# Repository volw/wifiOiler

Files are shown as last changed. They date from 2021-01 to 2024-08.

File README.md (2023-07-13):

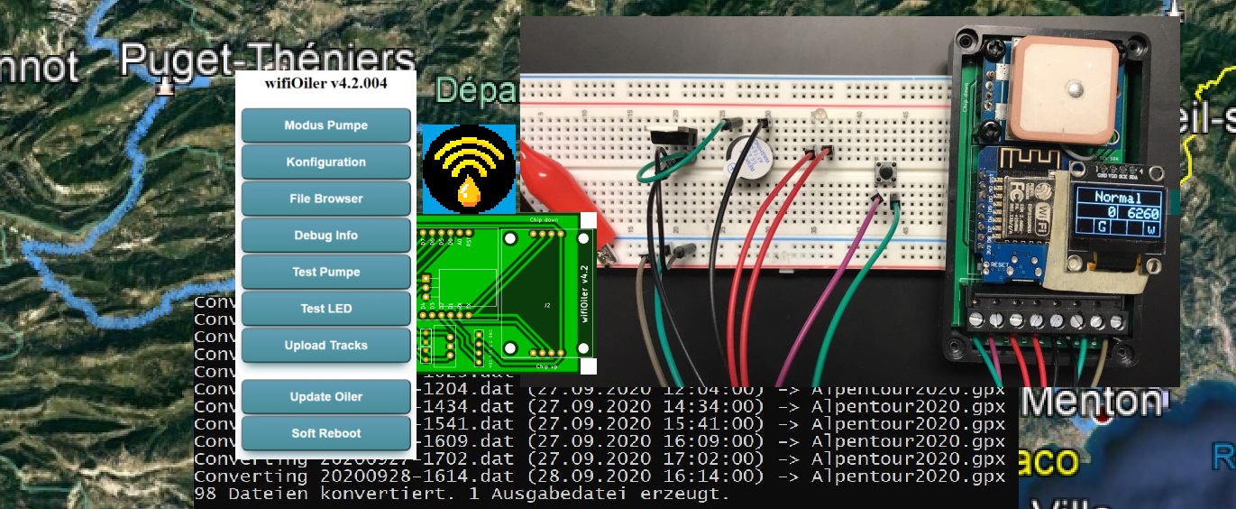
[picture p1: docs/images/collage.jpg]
wifioiler_collage


# wifiOiler

Automatischer streckenabhängiger Kettenöler für's Motorrad mit folgenden Funktionen:

- Ermittlung der zurückgelegten Strecke per GPS.
- Auslösen eines Ölvorgangs nach einer einstellbaren Anzahl von Metern.
- Drei verschiedene Distanzen oder Modi einstellbar (Normal, Regen, Offroad). 
- Notlaufprogramm = zeitabhängiges Ölen, falls kein GPS Signal empfangen werden kann.
- Bedienung über Button, Feedback per zweifarbiger LED.
- Erweiterte Bedienung über jedes internetfähige Gerät, auf dem ein Internet Browser läuft, z.B. Handy, Notebook, etc..
- Der Öler kann sich in ein bestehendes WLAN einklinken oder selber einen Access Point erstellen.
- WiFi kann jederzeit an- oder ausgestellt werden (während der Fahrt wird WiFi automatisch abgeschaltet).
- Aufzeichnung der gefahrenen Strecken im Speicher (LittleFS-Dateisystem) des verwendeten ESP8266 Chips (Platz für ca. 45 Stunden Fahrzeit vorhanden).
- Übertragen (und löschen) der aufgezeichneten Strecken per WLAN auf einen zentralen Web-Server (s. Oilerbase auf Basis eines Raspberry Pis, Strecken können auch manuell heruntergeladen werden).
- Herunterladen von Updates von einem zentralen Web-Server (s. Oilerbase). Updates können auch per Upload ausgelöst werden.
- PHP Skripte und html Dateien für den zentralen Web-Server (Apache auf Raspberry Pi, s. Oilerbase)
- Software zur Konvertierung der aufgezeichneten Tracks in das .gpx Format (können dann z.B. auf Google Earth angezeigt werden).

In diesem Repo zu finden:

- Schaltplan und Teileliste zur Erstellung und Bestückung der Platine.
- Vorschläge für Bauteile zum Einbau in das Motorrad.
- Komplette Software für Öler, Oilerbase und Track Konvertierung.
- Anleitungen für Aufbau, Inbetriebnahme und Bedienung (s. "docs").
- Einbauvorschlag.

Wem das alles zuviel an Bastelei ist und Hilfe bei Erstellung der Platine, bzw. Steuereinheit benötigt, kann sich gerne melden...

## Credits

Detlev Axon, creator of [RehOiler](https://www.rehtronik.de/startseite1.html)

Mikal Hart, creator of [TinyGPS++](https://github.com/mikalhart/TinyGPSPlus), an NMEA parsing library.

Hristo Gochkov for the FSBrowser example.

Maarten Lamers for his distance calculation (taken from TinyGPS++)

Patrick Gillespie for his [Macro Font Generator](http://patorjk.com/software/taag).

And many thanks to all the others who share their knowledge

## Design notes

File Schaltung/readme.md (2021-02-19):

# Schaltung

Die Schaltung wurde zuletzt mit KiCad 5.1.9_1 bearbeitet. Alle Symbole und Footprints wurden lokal verlinkt und sind in den Verzeichnissen enthalten (Symbole in wifiOilerLib.lib, Footprints in ProjectFootprints.pretty).

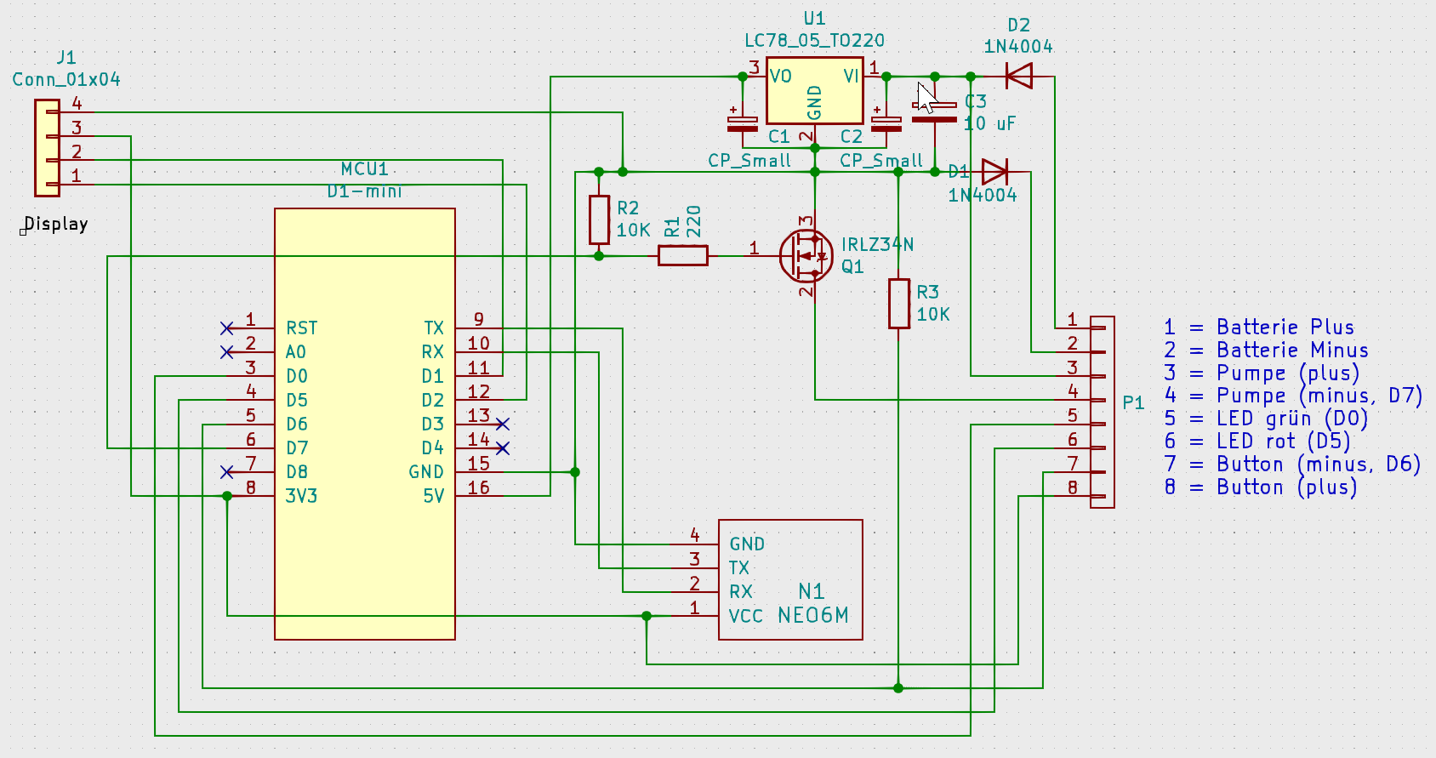
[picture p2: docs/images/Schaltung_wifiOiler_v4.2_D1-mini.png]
Schaltung wifiOiler v4.2 D1-mini


Abstände und Leiterbahnen wurden großzügig ausgelegt, um Fräsen und Löten zu erleichtern.

Noch ist eine Leiterbahn auf der zweiten Seite vorhanden, die aber auch noch eliminiert werden kann, wenn die Leiterbahnen, die zum Displayanschluss führen, etwas umgeroutet werden. Für eine Auftragsfertigung ist es fast egal, ob ein- oder zweiseitig, da viele Fertiger einseitige Platinen gar nicht mehr anbieten. Möchte man die Platine selber fräsen, sollte sie natürlich einseitig sein. Hier die Änderung, die dazu notwendig wäre (oben die aktuelle Ansicht, darunter die Änderung)

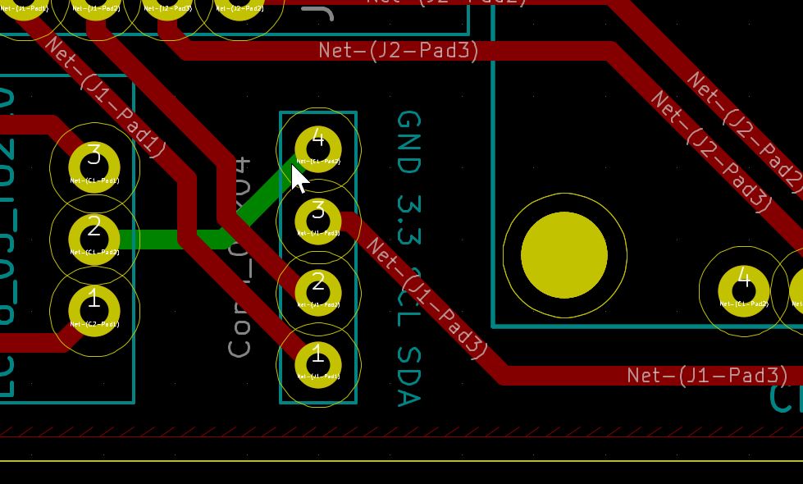
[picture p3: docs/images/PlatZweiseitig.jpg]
Platine zweiseitig
 

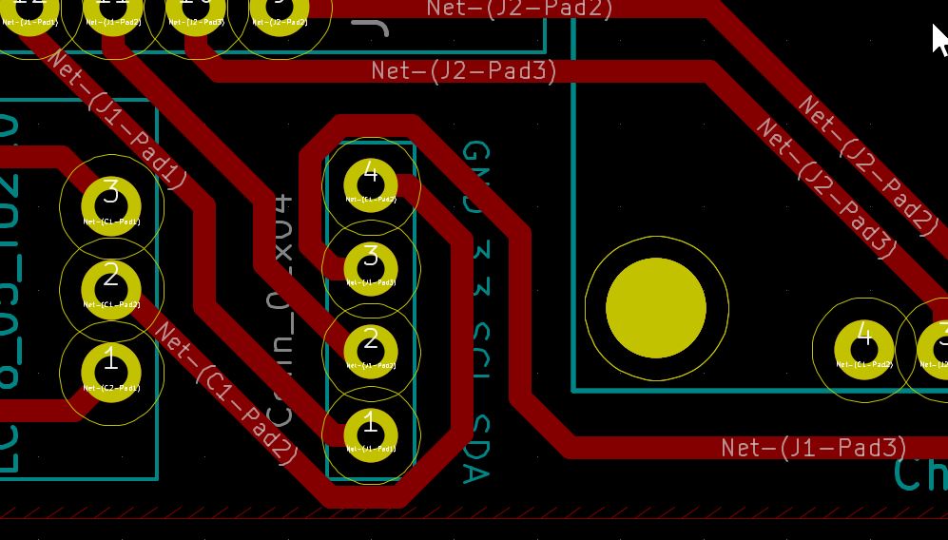
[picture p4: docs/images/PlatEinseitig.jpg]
Platine einseitig


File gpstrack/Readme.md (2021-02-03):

# wifiOiler GPX Converter

Die Fahrstrecken werden vom Öler in einem eigenen Format aufgezeichnet.

Mit diesem Tool können die Track-Dateien in das GPX Format konvertiert werden. Dann lassen sie sich z.B. in Google Earth anzeigen. Um das Projekt zu kompilieren, bzw. zu erstellen, wird Visual Studio benötigt (z.B. das kostenfrei nutzbare Visual Studio Community). 

**Syntax:** `gpstrack.exe [Quelle [Ziel]] [/o(verwrite)] [/d(aily)] [/r(ename)]`

Dabei bedeuten:

**Quelle:** ein Verzeichnis oder Suchmuster für Dateien, wie z.B. "D:\Touren\August" oder "202108*.dat". Wird als Quelle ein Verzeichnis angegeben, wird versucht, alle Dateien in diesem Verzeichnis mit der Endung .dat zu konvertieren.

**Ziel:** ist das Ziel ein existierendes Verzeichnis, werden die erzeugten .gpx Dateien in dieses Verzeichnis geschrieben. Existiert das Ziel dagegen nicht, wird als Ziel eine Datei angenommen und die Quelldateien werden in dieser Zieldatei zusammengefasst. Wenn kein Ziel angegeben wird, werden die Ausgabedateien in das Quellverzeichnis geschrieben.

**/o(verwrite):** wird diese Option angegeben, werden existierende Zieldateien ohne Nachfrage überschrieben. Die Option kann vollständig oder teilweise angegeben werden (also "/o" oder  "/overwrite" oder allen Zwischenformen).

**/d(aily):** wird diese Option angegeben, werden Dateien auf Tagesbasis zusammengefasst. Die Zieldateien haben als Namen das Tagesdatum in der Form JJJJMMTT.gpx. Diese Option hat keine Wirkung, wenn als Ziel eine Ausgabedatei angegeben wurde.

**/r(ename):** eigentlich nicht mehr relevant. In der Vergangenheit kam es schon mal vor, dass das Datum im Dateinamen vom ersten Datum in der Datei abwich. Diese Option hat das nachträglich korrigiert. War der Dateiname z.B: "000000-1435.dat", versucht das Programm, ein gültiges Datum in den GPS Daten in der Datei zu finden und den Dateinamen damit zu "reparieren".

### Beispiele

**`gpstrack`** alle Dateien im aktuellen Verzeichnis mit der Endung .dat werden konvertiert in Dateien mit der Endung .gpx.

**`gpstrack D:\temp /d`** alle Dateien im Verzeichnis D:\temp (mit Endung *.dat) werden auf Tagesbasis zusammengefasst und in das Verzeichnis D:\temp geschrieben (mit Endung .gpx)

**`gpstrack . Alpentour2020.gpx /o`** alle Dateien aus dem aktuellen Verzeichnis (s. den Punkt) werden in einer Zieldatei mit Namen "Alpentour2020.gpx" zusammengefasst. Falls die Datei schon existiert, wird sie überschrieben. Die Ausgabe dabei sieht etwa so aus (Ausschnitt):

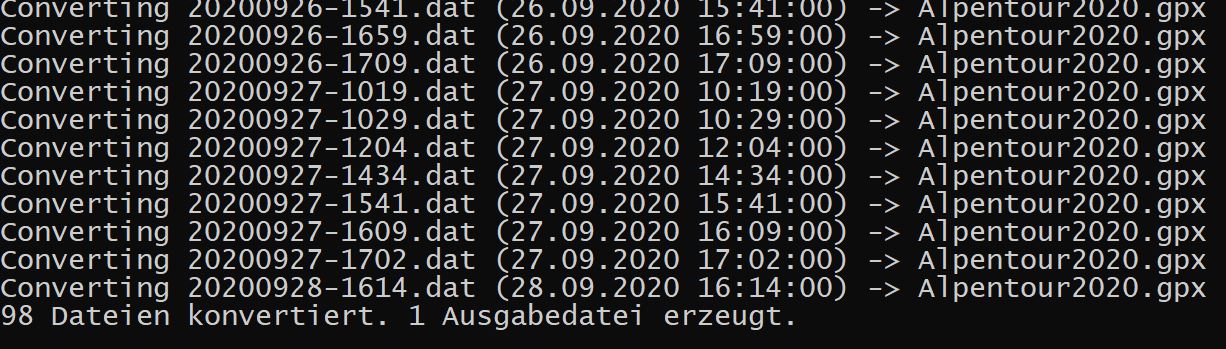
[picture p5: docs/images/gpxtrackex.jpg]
Ausgabe Alt-Text


Und das Ergebnis in Google Earth (beim Öffnen Dateityp .gpx wählen):

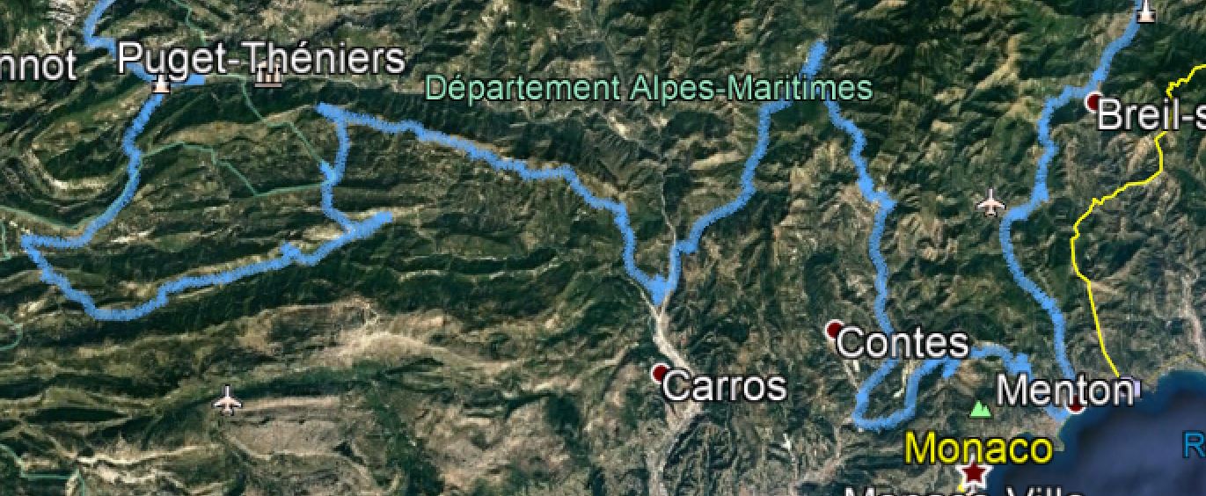
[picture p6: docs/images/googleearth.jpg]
Anzeige in Google Earth


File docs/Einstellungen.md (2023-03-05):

# Einstellungen
Hier werden die Einstellungen des Ölers beschrieben, die über die Web-Oberfläche geändert werden können. 
Die Einstellungen werden in der Datei **oiler.ini** in lesbarer Form gespeichert. 
Die Datei kann auch mit einem Editor bearbeitet werden, bevor sie hochgeladen wird. 
Geänderte Einstellungen, die über die Web Oberfläche geändert wurden, sind nach dem Speichern sofort aktiv. 
Dies gilt nicht für die Logging Einstellungen, die GPS-Konfigurationsdatei und die Einstellung für automatischen WiFi-Start. 
Um diese Einstellungen zu aktivieren, muss der Öler durchgestartet werden. 
Um geänderte Einstellungen zu aktivieren, die über den integrierten Editor geändert (oder mit der Upload-Funktion hochgeladen) wurden, muss der Öler neu gestartet werden.
<br>Folgende Einstellungen können angepasst werden:
## Wartezeit Simulation
Dieser Wert in Sekunden gibt an, ab wann das Notfallprogramm aktiv werden soll, wenn kein GPS Signal empfangen wird. Bei einem Wert von z.B. 180 wird 3 Minuten nach dem Start des Ölers (wenn bis dahin kein gültiges GPS Signal empfangen werden konnte) eine bestimmte Geschwindigkeit angenommen. Diese simulierte Geschwindigkeit wird durch den Wert **Meter/s bei Simulation** bestimmt. Beispielrechnung: wenn der Wert **Normal Mode Meter** 6000 beträgt und **Meter/s bei Simulation** 15, dann wird alle 400 Sekunden (3:40 min) gepumpt.
## Normal Mode Meter
Dieser Wert gibt in Metern an, nach welcher Strecke die Pumpe im Normalbetrieb aktiviert werden soll. Ein Wert von 6000 gibt also an, dass alle 6 km Öl an die Kette gegeben werden soll (Menge wird bestimmt durch **Anzahl Pumpaktionen pro Ölvorgang**).
## Rain Mode Meter
Wert in Metern, nach welcher Strecke auf nasser Straße die Kette etwas Öl bekommen soll.
## Offroad Mode Meter
Wert in Metern, nach welcher Strecke im Offroad-Betrieb die Kette geölt werden soll.
## Meter/s bei Simulation
Wird kein GPS Signal empfangen, wird nach einer festgelegten Zeit (s. **Wartezeit Simulation**) eine gewisse Geschwindigkeit angenommen, die durch diesen Wert bestimmt wird. Diese Simulation (oder Notfallprogramm) sorgt dafür, dass die Kette auch geölt wird, wenn aus irgendwelchen Gründen kein GPS Signal empfangen werden kann. Ein Wert von 15 z.B. (also 15 Meter pro Sekunde) simuliert eine Geschwindigkeit von 54 km/h (wird hinter dem Eingabefeld angezeigt). Oder anders gerechnet: im Modus Normal bei **Normal Mode Meter** von 6000 wird (6000 / 15 = 400) alle 400 Sekunden (also alle 3:40 Minuten) geölt.
## Anzahl Pumpaktionen pro Ölvorgang
Dieser Wert gibt an, wie oft die Pumpe pro Ölvorgang aktiviert werden soll. Bei der Dellorto Pumpe hat sich z.B. ein Wert von 3 bewährt (sonst kommt kaum was raus).
## GPS Low-Filter (cm)
Wert in cm, ab wann eine Bewegung als solche registriert werden soll. Hintergrund: das Signal vom GPS Modul 'streut' etwas, auch wenn die Karre nicht bewegt wird. Um diese Streuung rauszufiltern, ist dieser Wert gedacht. 500 (also 5 Meter) ist ein guter Wert.
## Öltank Kapazität
Anzahl an Pumpaktionen, bis der Tank leer ist. Dieser Wert ist leider nicht so gut zu schätzen. Bei jeder Pumpaktion wird auf jeden Fall die Anzahl Pumpvorgänge von diesem Wert abgezogen. Ist das Ergebnis unter 0, wird bei Start des Ölers ein LED Signal ausgegeben (mehrmaliges rot-grünes Blinken). Dies ist als Aufforderung zu verstehen, mal den Füllstand des Öltanks zu prüfen. Siehe auch **...davon verbraucht**.
## ...davon verbraucht
In diesem Feld werden alle Pumpaktionen seit dem letzten **reset** (s. Button neben dem Eingabenfeld) gezählt. Dies ist zusammen mit dem Wert **Öltank Kapazität** (s.o.) dafür gedacht, einen leer gelaufenen Öltank rechtzeitig zu erkennen. Überschreitet der Zähler den Wert **Öltank Kapazität** wird beim Start des Ölers ein LED Signal ausgegeben (mehrmaliges rot-grünes Blinken). Sieht man dieses Signal, sollte also der Füllgrad des Öltanks überprüft werden. Wurde der Öltank aufgefüllt, sollte dieser Zähler hier in den Einstellungen mit dem Button **reset** wieder auf 0 gesetzt werden.
## Name neuer Firmware Datei
Findet der Öler beim Start eine Datei mit diesem Namen, wird automatisch ein Update mit dieser Firmware Datei durchgeführt. Auch nachdem eine Datei manuell hochgeladen wurde, wird diese Prüfung (und ggf. ein Update) durchgeführt.
## Sek. zw. GPS Trackpoints
Dieser Wert gibt an, wie oft bei einer Streckenaufzeichnung ein Wegpunkt geschrieben werden soll. Einerseits möchte man die Strecke so genau wie möglich aufzeichnen - auf der anderen Seite ist der Speicherplatz halt begrenzt.
<br>Eigentlich ist es nicht unbedingt sinnvoll, jede Sekunde einen Wegpunkt aufzuzeichnen. Dadurch wird die Genauigkeit der aufgezeichneten Strecke auch nicht höher. Je schneller man fährt, um so gerader wird die Strecke wohl sein und nur bei vielen kleinen Kurven wäre eine höhere Genauigkeit wünschenswert (aber da fährt man im Allgemeinen auch keine 150).
<br>Ein Wert von 3 (also alle 3 Sekunden einen Wegpunkt schreiben) hat sich bewährt. Damit kann man ca. 46 Stunden Fahrt aufzeichnen. Ist der Speicherplatz vollständig belegt, wird die Aufzeichung automatisch gestoppt.
<br>Sollen die Touren überhaupt nicht aufgezeichnet werden, hier eine 0 einsetzen.
## eigener Host/Access Point Name
Name des Ölers und gleichzeitig des Access Points. Meldet sich der Öler in einem bekannten WLAN Netz an, ist das der Host Name, unter dem der Öler erreichbar ist, also z.B. **http://wifiOiler.local**. Kann der Öler sich an keinem WLAN anmelden, wird ein eigener Access Point/Hotspot mit diesem Namen erstellt. Auch hier wird nach erfolgter Anmeldung eine Verbindung über **http://<name>.local** hergestellt.
## Access Point Passwort
Passwort zur Verbindung mit Access Point.
## Upload Host Name
Host Name der Oilerbase, muss aus dem Internet erreichbar sein oder sich im gleichen Netz befinden. Siehe Dokumentation zur [Oilerbase](../OilerBase/readme.md).
## Upload Host Port
Port zum Upload der Track Dateien. Siehe Dokumentation zur [Oilerbase](../OilerBase/readme.md).
## Upload Host URL

URL für Upload der Track Dateien. Siehe Dokumentation zur [Oilerbase](../OilerBase/readme.md).

## Basic Authentication Zugangsdaten

Für den Zugang zur Oilerbase kann eine sogenannte "Basic Authentication" eingerichtet werden. Die notwendigen Zugangsdaten müssen hier dann in der Form <user>:<password> eingetragen werden, also z.B. "Peter:MeInPaSsWoRt". In der Einstellungsdatei oiler.ini wird dieser Wert mit der Javascript Funktion btoa() base-64 encoded abgespeichert. Falls man die Zugangsdaten in der oiler.ini manuell einfügt (also nicht über den Konfigurationsdialog des Ölers), muss die Codierung selber vorgenommen werden. Dafür gibt es Internetseiten (einfach mal nach "base64 Encoder" suchen). Mit den oben verwendeten Beispieldaten wird z.B. folgende Zeichenkette erzeugt: "UGV0ZXI6TWVJblBhU3NXb1J0".

Wird keine Basic Authentication an der Oilerbase verwendet, sollte dieses Feld leer gelassen werden.

## Logging to file?

Der Öler gibt während des Betriebs einige Diagnosemeldungen aus. Diese können zu Analysezwecken in eine Datei geschrieben werden. Es empfiehlt sich, dies nur kurzzeitig zu machen, da das interne Dateisystem schnell volllaufen kann. Im Regelfall steht hier also **Nein**.
## Logging to Serial?
Die Diagnosemeldungen des Ölers können während der Laufzeit über die serielle Schnittstelle ausgegeben werden. Dies ist ganz nützlich, um sie mit dem Arduino Serial Monitor mitzulesen, wenn man in der Bauphase ist oder die ersten Testläufe im nicht eingebauten Zustand macht. Ist der Öler erst mal eingebaut und sozusagen im Dauerbetrieb, sollte hier ein **Nein** stehen (auch wenn's den Öler nicht sonderlich stört, macht sich das in der Performance und ggf. im Stromverbrauch etwas bemerkbar).
## GPS Logging to File?
Die empfangenen GPS Daten können ebenfalls in eine Datei geschrieben werden (gpslog.txt). Zur kurzzeitigen Analsyse ganz nützlich - auf keinen Fall für längere Zeit auf **Ja** stehen lassen. Das Dateisystem ist ruckzuck voll, und der Öler wird stark ausgebremst. Also nicht stundenlang aktiviert lassen!!
## WiFi automatisch starten?
Gibt an, ob beim Starten des Ölers das WLAN automatisch aktiviert werden soll. Es kann auch nachträglich über den Button aktiviert werden (langer Buttondruck).

## GPS Track Filename Prefix
Hier kann für die Dateinamen, die für die Aufzeichnung von GPS Tracks verwendet werden, ein vorangestelltes Kürzel (Prefix) bestimmt werden. Die Dateinamen bestehen standardmäßig aus Datum und Uhrzeit des Aufzeichnungsstarts in der Form "JJMMTT-HHMM.dat". Ein Prefix ist z.B. dann sinnvoll, wenn mehrere Öler ihre aufgezeichneten Strecken auf eine Oilerbase hochladen. Mit dem Prefix "KTM-20" würde der Dateiname z.B. so aussehen: "KTM-20220818-1535.dat".

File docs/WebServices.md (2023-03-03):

# Web Services

Per HTTP Aufruf können einige Funktionen des Ölers aufgerufen werden.

| Link | HTTP Funktion | Rückgabe, Beschreibung |
| --- | --- | --- |
| /list?dir | HTTP_GET | JSON array mit allen Dateien, die sich im LittleFS befinden (type, name, size) |
| /list?tracks | HTTP_GET | JSON array mit allen aufgezeichneten Tracks (type, name, size). Eigentlich alle Dateien, deren Namen mit "2" anfängt. |
| /pumptest | HTTP_GET | "OK" (HTTP_RESULT 200, löst Pumpentest aus) |
| /ledtest | HTTP_GET | "OK" (HTTP_RESULT 200, löst LED-Test aus) |
| /config | HTTP_GET | JSON String mit allen Konfigurationswerten |
| /config?[Werte] | HTTP_POST HTTP_GET | Änderung des/der angegebenen Werte(s) (keine Fehlerbehandlung). <br/>Rückgabe: JSON String mit allen Konfigurationswerten<br/>Beispiel:<br />`curl http://wifioiler.local/config?nmm=8000&use=0` <br />ändert die Anzahl Meter für Modus "Normal" und setzt den Ölzähler zurück. |
| /pumpmode | HTTP_GET | Gibt aktuellen Modus der Pumpe zurück ("Normal", "Regen", "Offroad", "Permanent" oder "Aus") |
| /pumpmode?mode=\<mode> | HTTP_GET | Setzt Modus der Pumpe auf angegebenen Modus. "Normal", "Regen", "Offroad", "Permanent" oder "Aus" werden akzeptiert (Groß-/Kleinschreibung wird ignoriert). |
| /version | HTTP_GET | Gibt die aktuelle Version des Ölers zurück. |
| /edit | HTTP_POST | Hochladen einer Datei. Beispiel mit "curl": <br />`curl -v -F filename=config.htm.gz -F upload=@config.htm.gz http://wifiOiler.local/edit`<br />Download von Dateien mit "curl":<br />`curl http://wifioiler.local/index.htm.gz --output index.htm.gz`<br />Download mit gleichzeitigem unzip:<br />`curl http://wifioiler.local/index.htm.gz --output -\|gzip -d > index.htm` |
| /edit?file=\<filename> | HTTP_DELETE | Löschen der angegebenen Datei aus dem LittleFS Dateisystem. Name des Arguments beliebig. Beispiel:<br />`curl http://wifioiler.local/edit?file=index.htm`<br />VORSICHT: die angegebene Datei wird ohne Rückfrage unwiderruflich gelöscht. |
| /info | HTTP_GET | JSON Objekt mit runtime Informationen. Elemente des Objektes und ihre Bedeutung:<br />"ve" : aktuelle Softwareversion<br/>"da" : code für die Ansteuerung von Displays eingebunden?<br/>"rt" : Laufzeit des Ölers<br/>"bt" : Board Typ (Wemos mini, NodeMCU, etc.)<br/>"fr" : freier Hauptspeicher<br/>"cr" : Anzahl Zeichen, die vom GPS bis jetzt gelesen wurden<br/>"gf" : Anzahl GPS Sätze mit gültigem Fix<br/>"pc" : Anzahl GPS Sätze mit gültiger Prüfsumme<br/>"fc" : Anzahl GPS Sätze mit ungültiger Prüfsumme<br/>"mp" : Anzahl zurückgelegter Meter seit dem letzten Pumpvorgang<br/>"pm" : Aktuell eingestellter Modus der Pumpe<br/>"ra" : GPS Aufzeichnung eingeschaltet?<br/>"tf" : Name der aktuellen Track-Datei (nur vorhanden, wenn Aufzeichnung gestartet)<br/>"rw" : Anzahl der aufgezeichneten GPS Sätze<br/>"rs" : Größe eines GPS Satzes in bytes<br/>"we" : Anzahl an Schreibfehlern<br/>"gm" : Anzahl zurückgelegter Meter laut GPS<br/>"mc" : Aktueller Stand des movement Zählers<br/>"xc" : Max. möglicher Stand des movement Zählers<br/>"tc" : Anzahl Pumpvorgänge seit Start<br/>"mm" : Wartungsmodus aktiv?<br/>"wc" : SSID des WLANs mit dem der Öler aktuell verbunden ist<br/>"ip" : Aktuelle IP-Addresse<br/>"fs" : Freier Speicherplatz im Dateisystem (in bytes)<br/>"rl" : Anzahl GPS Sätze, die noch geschrieben werden können<br/>"tl" : Verbliebene Zeit für die Aufzeichnung (mit aktuell freiem Speicherplatz) |
| /reboot?bootnow | HTTP_GET | Neustart des Ölers. Da keine Rückgabe erfolgt, werden u.U. Fehlermeldungen von curl und ähnlichen Programmen ausgegeben. |

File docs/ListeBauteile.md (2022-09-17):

# Bauteilliste
Die meisten hier gelisteten Teile habe ich bei reichelt.de bezogen und verlinke sie auch entsprechend als Beispiel. Das tue ich, damit es keine Unstimmigkeiten bei der Beschaffung der Teile gibt. Dies soll keine Werbung für einen bestimmten Versender sein und ich bekomme auch keine Vergünstigungen dafür.
<br>

* 1 x Wemos (Lolin) D1 mini V2, die genaue Bezeichnung ist wohl "ESP8266 D1 Mini ESP-12F" [(Beispiel)](https://www.reichelt.de/d1-mini-esp8266-v3-0-d1-mini-p253978.html) 
* 1 x Spannungswandler auf 5V [(Beispiel)](https://www.reichelt.de/dc-dc-wandler-2-5-w-5-v-500-ma-to-220-lc78-05-0-5-p242823.html)
* 2 x Folienkondensator für Spannungswandler [(Beispiel)](https://www.reichelt.de/folienkondensator-100nf-63v-rm2-5-mks02-63-100n-p12314.html)
* 1 x Elko [(Beispiel)](https://www.reichelt.de/elko-radial-10-f-63-v-rm-2-0-85-c-2000h-20--rad-10-63-p15099.html)
* 1 x Mosfet IRLZ34N [(Beispiel)](https://www.reichelt.de/mosfet-n-ch-55v-30a-68w-to-220ab-irlz-34n-p41777.html)
* 1 x Widerstand 220 Ohm [(Beispiel)](https://www.reichelt.de/widerstand-metallschicht-220-ohm-0207-0-6-w-1--metall-220-p11627.html)
* 2 x Widerstand 10 KOhm [(Beispiel)](https://www.reichelt.de/widerstand-metallschicht-10-0-kohm-0207-0-6-w-1--metall-10-0k-p11449.html)
* 2 x Gleichrichterdiode (Verpolungsschutz) [(Beispiel)](https://www.reichelt.de/gleichrichterdiode-400-v-1-a-do-41-1n-4004-p1726.html)
* 2 x Stiftleiste (8) [(Beispiel)](https://www.reichelt.de/buchsenleiste-8-pol-gerade-rm-2-54-h-7-0-mm-bl-1x08g7-2-54-p180553.html)
* 2 x Stiftleiste (4) (oder: die 8er Leiste 3 x nehmen und eine in der Mitte durchtrennen)
* 1 x Stiftleiste (8) für Anschlüsse am Öler [(Beispiel)](https://www.reichelt.de/stiftleiste-fuer-anschlussklemme-8-polig-rm5mm-stl-017-08-p72099.html)
* 1 x Anschlussklemme für Anschlüsse am Öler [(Beispiel)](https://www.reichelt.de/steckbare-anschlussklemme-8-polig-rm5mm-akl-007-08-p72092.html)
* 1 x GPS Modul (siehe z.B. ebay) [(Beispiel)](https://www.ebay.de/itm/295106552762)
* 4 x Abstandsbolzen M3/6mm, für GPS Modul Montage auf Platine ([Beispiel](https://smile.amazon.de/Schrauben-Schraubenmutter-Sechskant-Distanzh%C3%BClsen-Aufbewahrungsbox/dp/B07KTZW5VL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))
* 1 x Universalgehäuse 85 x 50 x 29 [(Beispiel)](https://www.conrad.de/de/p/tru-components-tc-2028-sw203-1588521-modul-gehaeuse-85-x-50-x-29-abs-schwarz-1-st-1588521.html)
* Optional: 0.96 Inch OLED I2C Display [(Beispiel)](https://www.az-delivery.de/en/products/0-96zolldisplay)
* Ölpumpe, z.B. Dellorto Ölpumpe 12308 ([Beispiel](https://www.ebay.de/itm/Dellorto-Olpumpe-12308-/283344637971))
* 2 x Flachsteckerhülse für Anschluss der Pumpe ([Beispiel](https://www.reichelt.de/flachsteckerhuelse-breite-2-8mm-blau-fsh-b-2-8-p7907.html))
* 1 x Zweifarbige LED für Cockpit ([Beispiel](https://www.reichelt.de/duo-led-3-mm-bedrahtet-2-pin-rt-gn-14-mcd-60--led-3-rg-p10229.html))
* 1 x Einbaufassung für LED ([Beispiel](https://www.reichelt.de/einbaufassung-fuer-3-mm-leds-innenreflektor-schwarz-ebf-i-3-s-p7293.html))
* 1 x Button/Drucktaster  ([Beispiel](https://www.reichelt.de/drucktaster-ip67-sw-is-r3s-sw-p105682.html))
* Kabel zum Anschluss von LED und Button im Cockpit, sollte abgeschirmt sein ([Beispiel](https://www.reichelt.de/fernmeldeleitung-2-x-2-x-0-6-mm-5-m-ysty-2x2-5-p22965.html))
* Öltank aus dem Modellbau, Größe je nach verfügbarem Platz ([Beispiel](https://www.conrad.de/de/p/du-bro-404-kunstflugtank-120-ml-2190015.html)).
* KFZ-Flachsicherung ([Beispiel](https://www.reichelt.de/kfz-sicherung-normoto-3-a-violett-imaxx-f1503-p242048.html))
* KFZ Sicherungshalter ([Beispiel](https://www.reichelt.de/kfz-sicherungshalter-normoto-20-a-32-v-ip56-imaxx-h1325-p229033.html))
* Öl Auslassdüse am Kettenrad (hier am besten mal Ersatzteile bei kommerziellen Ölern checken). Es reicht auch ein dünnes, stabiles (ggf. schräg angeschnittenes Plastikröhrchen, sollte unten am Kettenrad enden, kurz über der Kette, damit die Schwungkraft das Öl zur Kette transportiert). Ist der Auslass, also der Durchmesser dieses Röhrchens zu groß, läuft u.U. der Ölschlauch leer, gerade wenn es im Sommer etwas heißer und das Öl "dünner" wird.
* Schläuche für Verbindung Tank - Pumpe und Pumpe - Auslass und vielleicht Schellen oder Klemmringe zur Befestigung der Schläuche. Die Dellorto Pumpe hat einen Eingang (Verbindung vom Tank kommend) mit 6,8 mm Außendurchmesser und einen Ausgang mit 3,5 mm Außendurchmesser. Der Schlauch von der Pumpe zur Auslassdüse am Kettenrad sollte schon etwas steifer sein (Hydraulikschlauch), da schlabbrige Schläuche in Ecken gelangen können, wo sie nichts zu suchen haben ;-) ([Beispiel für Schlauch (Ausgang Dellorto): 4 x 2,5](https://www.ebay.de/itm/264462877309))
* Befestigungsmaterial für Schläuche und Kabel zur Verlegung am/im Motorrad.
* Ggf. noch ein Ventil für den Entlüftungsschlauch am Tank. Durch heftige Schüttelbewegungen im Gelände kann eventuell durch den Entlüftungsschlauch Öl entweichen ([Beispiel](https://www.amazon.de/dp/B07CMRJ314/ref=pe_3044161_189395811_TE_SCE_3p_dp_1)).
#### Anmerkungen
* Die oben erwähnten Abstandsbolzen für die GPS-Modul Montage sind leider nicht wirtschaftlich zu beschaffen. Eigentlich kann man diese nur in Sortimentsboxen finden, die sich auch noch irgendwie viel zu teuer anfühlen (8-10,- Euro für eine Handvoll Plastik) und sehr wahrscheinlich nur teilweise gebraucht werden. Manchmal kann man solche Bolzen beim Auseinandernehmen von Elektroschrott finden. In der Größe M3 sind sie zwar etwas wuchtig, aber auch sehr stabil. M2 ist für die größeren Öffnungen im GPS-Modul schon fast zu klein. Kunststoff oder Messing ist Geschmacksache, man sollte aber daran denken, dass Messing leitfähig ist (noch besser als Zinn). Sehr passend sind hier M3 Varianten aus Kunststoff.

* Bei der Wahl der Kondensatoren und der entsprechenden Schaltung rund um den Spannungswandler gibt es vielleicht Optimierungsbedarf. Ich habe damit zu wenig Ahnung/Erfahrung und habe mir Teile der Schaltung im Internet zusammengesucht. Eins ist aber sicher: die Schaltung verrichtet bei mir seit drei Jahren einwandfreie Dienste. Vorschläge zur Optimierung nehme ich aber gerne entgegen. Anfangs habe ich übrigens lineare Spannungswandler (wie den LF50CV) verwendet - die wurden mir aber zu heiß.

* die 8er Stiftleiste durchzutrennen, um zwei 4er Leisten zu bekommen kann schon mal in die Hose gehen. Glatt in der Mitte zu brechen ist gar nicht so einfach. Wenn man es wirklich sauber haben will, bestellt man sich 4er Leisten. Ich persönlich bestelle immer 16er und breche/schneide sie zurecht.

* Als GPS Modul verwende ich die älteren aber sehr bewährten Neo-6M Module von u-blox. Die 8er Reihe habe ich auch schon getestet (in der Grundkonfiguration) und bin damit auch sehr zufrieden. Sicherlich kann man noch mehr aus den neueren Modulen herausholen. Für eine genauere Analyse fehlte mir aber bis jetzt die Zeit. Für die Auswahl ist aber wichtig, was auf dem verbauten u-blox Chip steht und nicht in der Artikelbeschreibung. Schon mehrfach habe ich gehört, dass das billigste Suchergebnis nicht unbedingt das war, was es versprach...

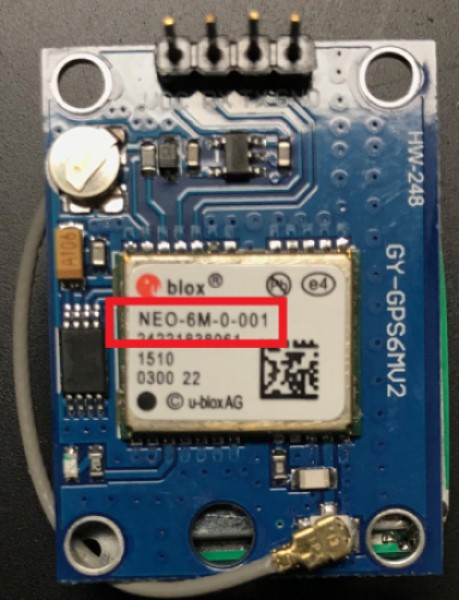
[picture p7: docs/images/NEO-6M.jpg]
NEO-6M
  

* Das Display ist mehr eine Spielerei. Eigentlich würde ich das gerne mit Button und LED am Lenker verbauen, habe aber bis jetzt kein passendes Gehäuse kaufen/herstellen können. Während der Bauphase liefert es aber nützliche Informationen, wie z.B. den eingestellten Pumpenmodus und ob GPS empfangen wird.
# Platine
Um eine passende Platine zu erstellen, gibt es verschiedene Möglichkeiten. Folgende habe ich ausprobiert:
### Tonerdirekttransfer
Man benötigt eine Platine, die einseitig mit Kupfer beschichtet ist und einen Laserdrucker. Mit dem Laserdrucker wird die Schaltung auf nicht zu saugfähiges Papier gedruckt (spiegelverkehrt). Der Ausdruck wird nun auf die Platine gelegt, sorgfältig fixiert, mit einer Aceton/Alkohol Lösung getränkt und fest auf das Kupfer der Platine gepresst (am besten mit einer Andruckrolle). Ist das Aceton und der Alkohol verflogen, entfernt man das Papier und siehe da: die Schaltung in Form des Toners befindet sich nun auf der Kupferschicht der Platine. Fehlerhafte Stellen können nun mit einem permanenten Edding Stift ausgebessert werden. Danach wird das überflüssige Kupfer mit Säure abgewaschen (entweder im Säurebad oder mit einem kleinen Schwamm). Zum Schluss müssen noch die Bohrlöcher gesetzt werden (Bohrständer setze ich mal voraus - so aus der Hand ist das nahezu unmöglich). Mit ein wenig Übung lassen sich so in Heimarbeit in kurzer Zeit nutzbare Platinen herstellen.
<br>Hinweis: zu den einzelnen Arbeitsschritten gibt es im Internet unzählige Informationen.

### Portalfräse
Mit einer einfachen (Portal-)Fräse lassen sich natürlich auch Platinen herstellen - die Isolationsbahnen werden einfach ausgefräst. Und das Bohren muss hier nicht manuell durchgeführt werden, auch das wird mit der richtigen Software erledigt. Bis der Workflow ausgetüftelt ist und die Einstellungen richtig gesetzt sind, dauert es sicher ein wenig (wenn man den Verlust einiger Platinen und Stichel/Bohrer verkraften kann). Aber auch dann kann innerhalb kurzer Zeit ohne Fremdhilfe eine Platine erstellt werden.
### Auftragsfertigung
Zum Schluss habe ich mal einen chinesischen Fertiger ausprobiert, der mit einem unglaublichen Angebot lockte (5 Platinen für 2$). Auf der entsprechenden Web-Seite lädt man den Schaltplan (bzw. die sogenannten Gerber Dateien) hoch, konfiguriert die Fertigungsmethode (z.B. bleifreie Beschichtung, was natürlich mehr kostet) und wartet dann auf das Ergebnis. Die letzte Bestellung (10 Platinen) dauerte incl. Versand genau 7 Tage und kostete 6,23€ für die Platinen und 8,19€ für den Versand (FedEx Intl. Priority), insgesamt 14,42€ - also knapp einsfuffzich pro Platine. Ehrlich gesagt, kann man's dafür nicht selber machen. Zugegeben, die 7 Tage (per FedEx) waren schon besonders. Für weniger Porto (z.B. 5,31€) kann die Wartezeit schon mal länger werden (angeblich 3 Wochen, bei mir waren's schon mal 6). Das Ergebnis kann sich auf jeden Fall sehen lassen:
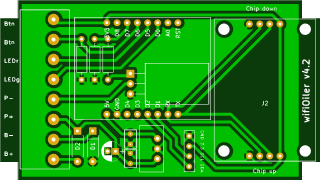
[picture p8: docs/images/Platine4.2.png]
Platine
<br>

Ein paar Platinen habe ich übrigens noch und verschenke diese (jeweils eine). Wer Interesse hat, PM an volw (at) gmx (punkt) de. 

Der in KiCad erstellte Schaltplan ist auch hier zu finden. Eine Anleitung zum Erstellen der notwendigen Dateien gibt es bei den Herstellern gewöhnlich auf deren Internetseite [(Beispiel)](https://support.jlcpcb.com/category/23-technical-support).
<br><br>Es gibt natürlich Gründe, warum man vielleicht woanders bestellen sollte - das muss jeder mit sich selbst ausmachen.

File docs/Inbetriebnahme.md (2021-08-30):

# Inbetriebnahme und Einbau

Um die Software zu kompilieren und auf den "Wemos D1 mini" (s. Teileliste) oder allgemein SoC (System on a Chip) zu laden, sind folgende Schritte notwendig. Eventuell könnt ihr einige Schritte überspringen, je nachdem, ob ihr schon mal mit einem D1 Mini oder einem anderen Microcontroller gearbeitet habt, der auf einem ESP8266 (ursprünglich von der Firma espressif) basiert.

Alle hier beschriebenen Tätigkeiten sind Vorschläge, die je nach Installation auch mal anders ausfallen können. An dieser Stelle sei nochmal erwähnt, dass keine Gewährleistung für irgendwelche Schäden übernommen werden. Alle Tätigkeiten geschehen auf eigenes Risiko.

## Arduino Entwicklungsumgebung

Die Entwicklungsumgebung wird ab jetzt der Einfachheit halber IDE genannt. Hier wird die Installation und Inbetriebnahme der portablen Version beschrieben. Benutzt man die für Windows vorgesehene Installationsversion sind ggf. andere Verzeichnisse wichtig, die hier nicht beschrieben werden.

- IDE herunterladen und dabei Windows ZIP file wählen ([Link](https://www.arduino.cc/en/software)) 
- den in der Zip-Datei enthaltenen Ordner an einen sicheren Platz kopieren, mein Beispiel: "F:\apps". Nach dem entpacken sollte es also einen Ordner "F:\apps\arduino-1.8.13" geben (bzw. mit einer höheren Versionsnummer).
- In diesem Verzeichnis, neben den anderen bereits enthaltenen Ordnern, einen Ordner mit Namen "portable" anlegen. Nach unserem Beispiel also "F:\apps\arduino-1.8.13\portable". Damit wird der IDE gesagt, dass es sich um eine sogenannte portable Installation handelt. 
- Die im Verzeichnis "F:\apps\arduino-1.8.13" enthaltene arduino.exe starten. Eventuell kommt eine Meldung der Windows Firewall, dass "einige Features dieser App blockiert wurden". Unter Pfad wird der Windows Java Interpreter angegeben, der mit der Arduino IDE gekommen ist (nach unserem Beispiel: "F:\apps\arduino-1.8.13\java\bin\javaw.exe"). Diese Meldung kann mit "Zugriff zulassen" beantwortet werden.
- Um die Arduino IDE für die Programmierung von ESP8266 basierten SoCs vorzubereiten, starten wir in der IDE den Einstellungsdialog, im Menü zu finden unter "Datei" -> "Voreinstellungen". Im unteren Teil des Fensters findet sich ein Eingabefeld "Zusätzliche Boardverwalter-URLs:". Hier wird folgender Link eingetragen: https://arduino.esp8266.com/stable/package_esp8266com_index.json. Dann den Dialog mit "OK" bestätigen.
- Dann die Boardverwaltung aufrufen, zu finden im Menü unter "Werkzeuge" -> "Board: ..." -> "Boardverwalter". Im oberen Eingabefeld "ESP8266" eingeben. Es sollte ein Treffer "esp8266" und darunter "by ESP8266 Community" angezeigt werden. Diesen Treffer anwählen, bzw. "Installieren" wählen. Die Installation kann ein wenig dauern. Wenn man danach einen Blick in das "portable" (s.o.) Verzeichnis wirft, sollten dort einige Unterverzeichnisse und Dateien zu finden sein, wie "sketchbook" oder "packages".

#### LittleFS Uploader

Um ein LittleFS Dateisystem auf dem SoC einzurichten und zu nutzen, bzw. Dateien dorthin hochzuladen, kann ein Upload Tool in die Arduino IDE integriert werden. Es lädt auf Knopfdruck alle Dateien hoch, die sich im Unterverzeichnis "data" eines Sketches befinden.

- Im Verzeichnis "sketchbook" ein Unterverzeichnis mit Namen "tools" anlegen (nach unserem Beispiel: "F:\apps\arduino-1.8.13\sketchbook\tools").
- Von der github Seite [LittleFS Upload Tool](https://github.com/earlephilhower/arduino-esp8266littlefs-plugin/releases) das aktuellste Release herunterladen und das in der Zip-Datei enthaltene Verzeichnis in das tools Verzeichnis kopieren. Das Ergebnis sollte nach unserem Beispiel etwa so aussehen: "F:\apps\arduino-1.8.13\portable\sketchbook\tools\ESP8266LittleFS\tool". In diesem Verzeichnis befindet sich das eigentliche tool "esp8266littlefs.jar" (Stand Februar 2021).
- Nun die Arduino IDE beenden und wieder starten. Im Menü sollte der Eintrag "Werkzeuge" -> "ESP8266 LittleFS Data Upload" zu finden sein.

#### Benötigte Bibliotheken installieren

Um die Öler Software erfolgreich zu kompilieren, benötigen wir noch einige Bibliotheken:

- Adafruit SSD1306 Library (für die Ansteuerung des Displays): in der Arduino IDE über das Menü "Werkzeuge" -> "Bibliotheken verwalten", nach "adafruit ssd1306" suchen und diese installieren. Erscheint eine Meldung, dass noch andere abhängige Bibliotheken existieren ("Would you like to install also all the missing dependencies?)", bitte "Install all" wählen. 
- TinyGPS++ Library: diese Lib ist aktuell nicht über die Bibliotheksverwaltung installierbar. Herunterladen kann man sie von der [github Seite von Mikal Hart](https://github.com/mikalhart/TinyGPSPlus) Habt ihr die Zip-Datei heruntergeladen, extrahiert ihr den enthaltenen Ordner in das "portable\sketchbook\libraries" Verzeichnis. Danach müsste das nach unserem Beispiel so aussehen: "F:\apps\arduino-1.8.13\portabe\sketchbook\libraries\TinyGPSPlus-master" (das "-master", welches von github angehängt wird und den branch bezeichnet, bitte entfernen).
- Wird die IDE nun beendet und wieder gestartet, können im Menü unter "Datei" -> "Beispiele" -> "TinyGPS++" einige Beispiel Sketches gefunden werden.

#### Software kompilieren und hochladen

Nun sind alle Voraussetzungen erfüllt und wir können den "Wemos D1 mini" mit einem Micro-USB Kabel anschließen. In der Arduino IDE sind nun folgende Werte festzulegen:

- Werkzeuge -> Board -> ESP8266 Boards (...) -> LOLIN (WEMOS) D1 R2 & mini

- Werkzeuge -> Flash Size -> 4MB (FS:**3MB** OTA:~512KB)
- Werkzeuge -> Port: (hier den richtigen USB Port wählen)

Wird kein Port zur Auswahl angeboten, muss wahrscheinlich noch ein "USB to Serial Port" Treiber installiert werden. Auch daran zu erkennen, dass im Windows Gerätemanager unter "Andere Geräte" ein "USB2.0-Serial" Gerät mit gelbem Warndreieck angezeigt wird.

Den Treiber findet man z.B. hier beim [Hersteller](http://www.wch-ic.com/downloads/CH341SER_ZIP.html). Nach erfolgreicher Installation sollte im Gerätemanager unter "Anschlüsse (COM & LPT)" ein Gerät mit der Bezeichnung "USB-Serial CH340 (COMx)" angezeigt werden. Den angezeigten COM-Port in Klammern auch in der Arduino IDE wählen.

Jetzt kann kompiliert werden: Sketch -> Überprüfen/Kompilieren. Sollte fehlerfrei durchlaufen, ansonsten Meldungen im unteren Teil der IDE beachten.

Vor dem Hochladen der Dateien und des Programms, bitte die Datei **wifi.ini** im Unterverzeichnis **data** des Sketches anpassen und dort die eigenen WiFi/WLAN Daten eingeben. Der Sketch Ordner lässt sich einfach über das Menü in der IDE öffnen: "Sketch" -> "Sketch-Ordner anzeigen".

Nun die folgenden Schritte ausführen, um das LittleFS zu füllen und die Firmware, bzw. das Programm zu übertragen:

- Werkzeuge -> ESP8266 LittleFS Data Upload (häufiger Fehler: serieller Monitor ist geöffnet)
- Sketch -> Hochladen

Nachdem der Sketch hochgeladen wurde, wird der Sketch zwar sofort gestartet, man sieht aber nicht so viel. Dazu nun den seriellen Monitor starten und unten auf 9600 Baud einstellen. Den seriellen Monitor findet man in der IDE über "Werkzeuge" -> "Serieller Monitor". Den "Wemos D1 mini" eventuell über den Reset Knopf neu starten. Die Ausgabe im seriellen Monitor sollte dann etwa so aussehen:

> ```
> ⸮$N⸮h⸮HdCZ⸮⸮B`⸮⸮
> 166:********** Starting...
> 166:[checkforUpdate] Looking for firmware file /wifiOiler.ino.d1_mini.bin
> 170:[checkforUpdate] no new firmware found
> 220:LittleFS free: 2820096 bytes = 52224 GPS records (43:31)
> 609:[setupGPS] calling configureGPS()
> 609:[configureGPS] still under construction...
> 609:reading gps device config file /Neo-M6.ini
> [...]
> 942:This is wifiOiler version 4.2.011 on board WemosMini
> 943:starting WiFi ...
> 1124:Versuche, mit bekanntem Wifi Netz zu verbinden...
> 1211:Add wifi to wifiMulti: HandyHotspot
> 1212:Add wifi to wifiMulti: SweetHomeWLAN
> 1213:Connecting Wifi .....
> 5077:WiFi connected to 'SweetHomeWLAN' - IP address: 192.168.178.42
> 5179:mDNS responder started, please connect to "http://wifiOiler.local"
> 5599:-------- Initialisierung beendet.
> ```

Mit der Software können nun die ersten Versuche gestartet werden. Dazu den Browser öffnen und mit "http://wifiOiler.local" verbinden. 

## Platine

Tipps zur Erstellung der Platine sind im Dokument "ListeBauteile" zu finden. Wer noch nicht so oft gelötet hat, hier einige Tipps:

- die Oberfläche der Platine sollte blank, sauber und korrosionsfrei sein. Wenn z.B. eine kupferbeschichtete Platine etwas länger liegt, bilden sich Ablagerungen, die die Annahme von Lötzinn erschweren. Ggf. mit einem Topfschwamm oder leicht schleifenden Mitteln bearbeiten (aber Vorsicht: nicht gleich das ganze Kupfer abschleifen!), ggf. mit Aceton reinigen.
- in gut belüfteten Räumen arbeiten. Auch wenn das Lötzinn (Lot) heutzutage nicht mehr mit Blei versetzt ist (oder sein sollte), sind die entstehenden Dämpfe bestimmt nicht gesund.
- als erstes die flachen Teile auflöten (in diesem Fall die Gleichrichterdioden und die Widerstände) und sich dann langsam "hocharbeiten". Zum Schluss die höchsten Teile, sollte in diesem Fall der Elko sein. Ggf. können die Bauteile während des Lötens mit Klebeband fixiert werden, damit sie beim anlöten auch richtig sitzen.
- Es muss kein teurer Lötkolben sein, geregelt wäre aber schön und die Lötspitze sollte nicht zu dick sein (also nicht der Breitmeißel für die Dachrinne).
- Nicht zu dickes Lötzinn verwenden. Dünneres kann besser dosiert werden. Bei diesen Bauteilen verwende ich Lot mit einem Durchmesser von 0,8-1mm.
- Das GPS Modul kann auf zwei Arten angeschlossen werden, Chip-up oder Chip-down, je nachdem, wo die Antenne verbaut wird. Am besten klebt man sie mit doppelseitigem Klebeband auf die Rückseite des GPS-Moduls und verbaut dieses Chip-down, also so, dass der u-blox Chip auf dem GPS-Modul nach unten zeigt. Wenn dies so geplant ist, dann die zweite Steckbuchsenleiste für Chip-Up Installation weglassen (kollidiert sonst etwas mit dem Antennenanschluss). Die beiden Anschlüsse sind an der Beschriftung auf dem Schaltplan/Platine zu erkennen.
- Zum Schluss den betankten "Wemos D1 mini" (s.o. "Software kompilieren und hochladen") in die dafür vorgesehenen Buchsenleisten stecken (USB Buchse zur Anschlussleiste)

Hier noch ein Foto eines Versuchsaufbaus (mit angeschlossenem Display):

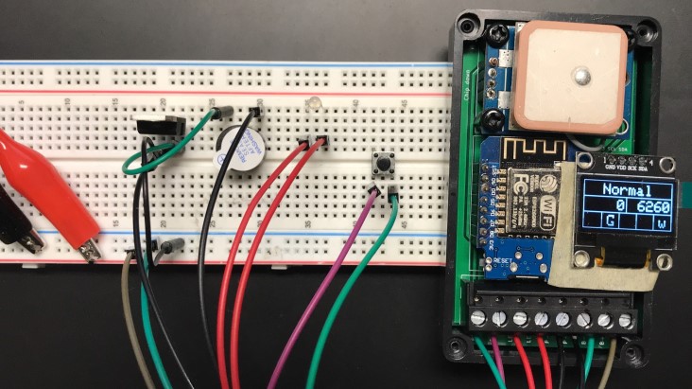
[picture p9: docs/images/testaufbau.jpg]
Testaufbau


## Einbau Motorrad

Jetzt geht es an den Einbau. Schon vorab sollte man sich überlegen, wo Platz für Pumpe, Öltank und Öler sein könnte. Danach richten sich u.U. die benötigten Kabel- und Schlauchlängen.

#### Einbau Button und LED im Cockpit

Für den Einbau könnte ein Ausbau des entsprechenden Cockpit-Teils notwendig, bzw. nützlich sein. Es müssen Löcher für den Einbau der LED Fassung und den Button geschaffen werden. Die LED in der Fassung ggf. mit einem Stück Platine kontern und anlöten. Da die vorgeschlagenen Kabel, bzw. die Litzen im Kabel sehr dünn sind, ist das Befestigen der LED etwas fummelig. Für den Button können evtl. auch kleine Stecker nützlich sein. Bei einer frei schwebenden Verlötung können mechanische Belastungen die dünnen LED Anschlüsse schnell brechen lassen. Die großzügige Verwendung von Klebeband schützt so eine Installation enorm ;-). Das Verbindungskabel zum Öler "schlabberfrei" verlegen, damit es nicht in bewegliche Teile gerät (ggf. mit Kabelbindern befestigen).

#### Öltank

Den Öltank so anbringen, dass die Öl-führenden Auslässe im Öl liegen und der Entlüftungsstutzen eben nicht. Eine etwas besser zugängliche Stelle ist nützlich (z.B. unter der Sitzbank, wenn möglich). Der Entlüftungsschlauch sollte höher enden, als die Einbauposition des Tanks. Trotzdem ist ein Ventil für den Entlüftungsschlauch sinnvoll. So kann mit Sicherheit vermieden werden, dass durch den Entlüftungsschlauch austretendes Öl die Karre einsaut. Das Befüllen des Tanks sollte schon vor dem endgültigen Einbau erfolgen. Zum Be- oder auch Nachfüllen eignet sich eine Einmalspritze ganz gut (in jeder Apotheke erhältlich). Vorsicht: mit der Spritze kann gut ein Überdruck im Tank erzeugt werden - und das Öl kommt zurück, sobald es die Gelegenheit hat.

Welches Öl man verwendet, ist Geschmacks- und Glaubenssache. Persönlich verwende ich gutes Sägekettenöl. Viskosität und Haftung ist gut und es kostet nicht so viel.

#### Pumpe

Die Pumpe am besten in der Nähe des Tanks installieren, um die Länge der ölgefüllten Schläuche zu verringern. Nur sicherstellen, dass die Schläuche nicht geknickt werden.

#### Auslassdüse

Die Verlegung des Schlauchs von der Pumpe zum Auslass unbedingt **sicher** gestalten. Der Schlauch hat ohne eine sichere Befestigung nichts in der Nähe von beweglichen Teilen zu suchen. Manchmal besteht die Möglichkeit, den Schlauch **durch** die Schwinge direkt bis zum Kettenrad zu verlegen - dort ist er natürlich gut aufgehoben. Ansonsten helfen kleb- oder schraubbare Kabelführungen, Schlauchschellen, Kabelbinder, etc.. Die Schläuche selber müssen natürlich Öl-beständig sein. Der Schlauch zum Auslass sollte etwas steifer ausfallen (Pneumatik Schlauch, Durchmesser s. Auslass Ölpumpe). 

Die Auslassdüse so anbringen, dass sie direkt am Kettenrad kurz über der Kette endet, und zwar so, dass das austretende Öl per Fliehkraft an/in der Kette landet (am besten also mittig unten "bei 6 Uhr"). Die angeschrägte Austrittsöffnung dabei nach außen drehen, damit beim rückwärts rangieren nicht so schnell Dreck in die Düse geschoben wird.

Sitzt der Ausgangsschlauch, diesen oben an der Pumpe nochmal lösen und mit Öl füllen, bis es unten raustropft (etwas unterstellen). Nicht zu viel Luft im Schlauch lassen.

#### Öler

ACHTUNG: hier wird mit Strom hantiert - bitte unbedingt Sicherheitshinweise eures Fahrzeugs beachten. Die hier beschriebene Vorgehensweise geschieht auf eigene Gefahr. Es wird selbstverständlich keine Haftung in jeglicher Art übernommen. Diese Anleitung ist nur ein Vorschlag.

Der Stromanschluss des Ölers wird an Zündung plus abgenommen (oft vorne und hinten vorhanden, ggf. Schaltplan konsultieren, Sicherung zwischenschalten). Das Gehäuse des Ölers muss nicht unbedingt angeschraubt werden - ein Regen- und Spritzwasser geschütztes Plätzchen ist aber sinnvoll. Zur Vorsicht kann der Öler z.B. auch in einen Gefrierbeutel gesteckt/gewickelt werden, da (den Einsatz des vorgeschlagenen Spannungswandlers vorausgesetzt) im Betrieb so gut wie keine Hitze entsteht. Zusätzlich schützt etwas Schaumstoff gegen zu heftige Erschütterungen. Vor dem Einbau sollte aber unbedingt die Erreichbarkeit über WLAN sichergestellt werden. Die erstmalige Programmierung **muss im ausgebauten Zustand** erfolgen (s.o.).

Der Empfang des GPS Moduls ist mit der verwendeten Keramik Aktivantenne recht ordentlich. Unter dem Sozius verbaut, dauert es bis zum ersten Fixpunkt wenige (bis max. ca. 30) Sekunden.

#### Einschalten und Test

Ist alles an Ort und Stelle, kann nun die Zündung eingeschaltet werden. Die LED im Cockpit sollte grün für einige Sekunden leuchten und dann entweder mehrmals kurz grün blinken (mit konfiguriertem WLAN verbunden) oder erst dreimal kurz rot, dann dreimal kurz grün blinken (Access Point erstellt).

Ist jetzt z.B. das Handy mit dem gleichen WLAN verbunden, kann per Browser gleich auf den Öler zugegriffen werden. Wurde der Name des Ölers in der Konfigurationsdatei "oiler.ini" nicht geändert, dann lautet die Adresse "http://wifioiler.local".

Wurde eine Access Point erstellt, dann erst mit diesem verbinden und ebenfalls o.g. Adresse verwenden. Damit sollte man im Hauptmenü des Ölers landen und kann nun einen LED- oder Pumpentest auslösen.

#### Entlüften

Zum Schluss die Pumpe auf Dauerbetrieb stellen, bis unten Öl aus dem Auslass kommt.

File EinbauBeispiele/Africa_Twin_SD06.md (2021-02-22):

#### Einbaubeispiel 

# Africa Twin SD06 DCT

Vorne im Cockpit fand sich schnell ein Plätzchen für den Button und die LED (sorry, etwas unscharf):

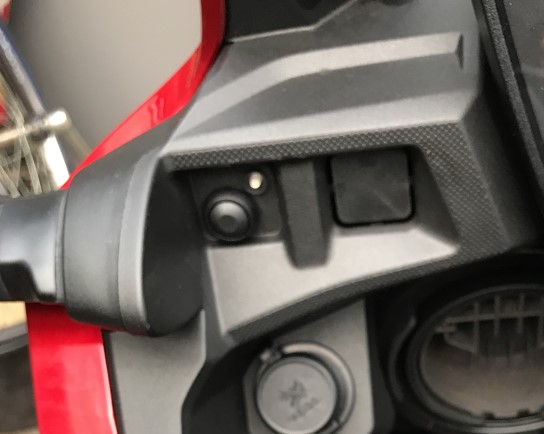
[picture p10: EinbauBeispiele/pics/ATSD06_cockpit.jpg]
ATSD06_cockpit


Für die Montage musste allerdings das halbe Fahrzeug auseinandergebaut werden. Zum Glück gab es viele hilfreiche Anleitungen auf youtube (Seiten- und Frontverkleidung Ab- und Anbau).

Öltank und Pumpe wurden unter dem Fahrersitz untergebracht, der Öler unterm Sozius. Stromabnahme hinten links (direkt ans Kabel gelötet - es soll aber auch Stecker geben...).

Der Ölschlauch von der Pumpe zum Auslass wurde durch die Schwinge gezogen (hier ein Foto vom vorderen Eingang):

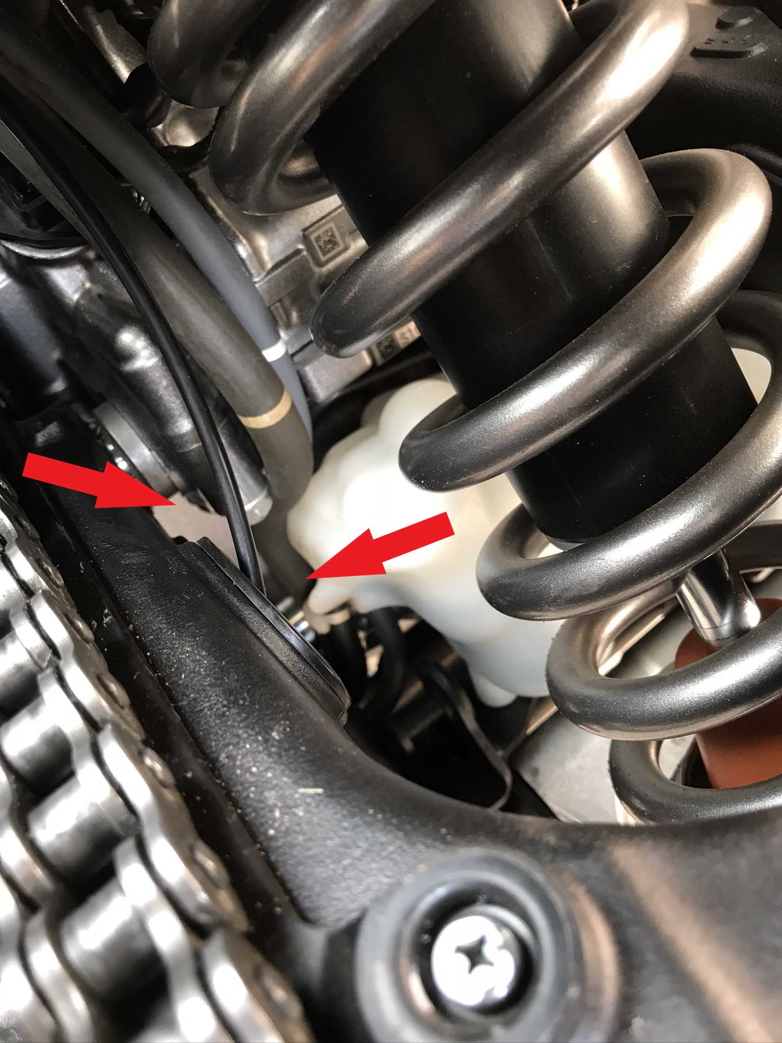
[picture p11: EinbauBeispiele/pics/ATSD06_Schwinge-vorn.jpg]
ATSD06_Schwinge-vorn


Hinten dann passend hinter dem seitlichen Kettenschutz der Auslass aus der Schwinge. Die Auslassdüse wurde dort mit einer Trägerplatte unten an die Schwinge geschraubt und dann so ausgerichtet, dass sie kurz über der Kette ziemlich dicht am Kettenrad endet (nicht so gut zu sehen). Eine kleine Schlauchschelle hält den Schlauch und die Düse (hier noch mit einem Stück größerem Schlauch umgeben) an der Trägerplatte:

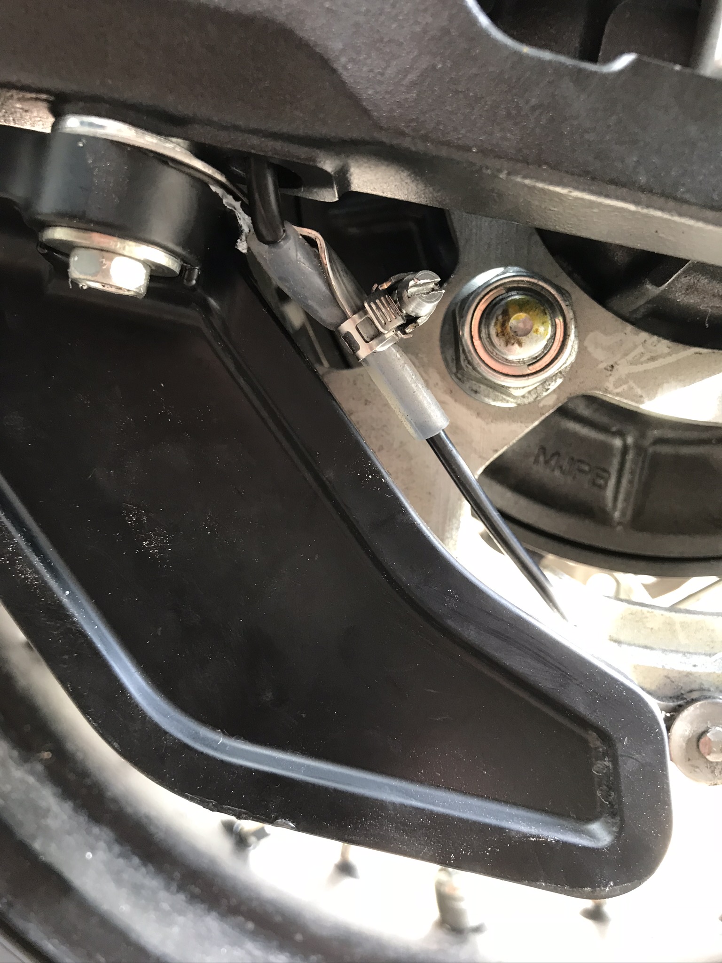
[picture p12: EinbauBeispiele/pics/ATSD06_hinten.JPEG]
ATSD06_hinten


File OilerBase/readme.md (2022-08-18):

# Oilerbase
Die sogenannte Oilerbase ist ein Raspberry Pi mit einem Apache Web-Server, der zwei Funktionen zur Verfügung stellt.
- Vom Öler aufgezeichnete Fahrstrecken (Tracks) können per Knopfdruck hochgeladen werden, um die Tracks zuhause zu sichern und Speicherplatz auf dem Öler freizugeben. Bei intensiver Nutzung sollte man das alle 1-2 Wochen machen - es können aber mehr als 40 Stunden Fahrzeit aufgezeichnet werden, ohne die Tracks hochzuladen. Ist der Speicherplatz erschöpft, wird die Aufzeichnungsfunktion automatisch deaktiviert.

- Außerdem können auf der Oilerbase Updates bereitgestellt werden, die mit der integrierten Update-Funktion des Ölers heruntergeladen und eingespielt werden können. So können selbst Anpassungen am Öler vorgenommen und diese leicht eingespielt werden.

## Inhalt  
- [Benötigtes Zubehör](#Benötigtes-Zubehör)
- [Betriebssystem installieren](#Betriebssystem-installieren)
- [Apache Web Server installieren](#Apache-Web-Server-installieren)
	- [Installation des Apache Web-Servers](#Installation-des-Apache-Web-Servers)
	- [Apache Web Server absichern](#Apache-Web-Server-absichern)
	- [Verzeichnisstruktur einrichten](#Verzeichnisstruktur-einrichten)
- [Installation von Samba](#Installation-von-Samba)
	- [Verzeichnis unter Windows einbinden](#Verzeichnis-unter-Windows-einbinden)
- [Öler testen](#Öler-testen)
- [Oilerbase veröffentlichen](#Oilerbase-veröffentlichen)

### Benötigtes Zubehör

Folgende Dinge werden benötigt, um eine Oilerbase aufzubauen und zu betreiben:

- 1 Raspberry Pi, (z.B. ein RPi 3 Modell B+) plus passendes Netzteil.
- eine MicroSD Card, Empfehlung: 16GB.
- möchte man die Oilerbase nutzen, wenn man länger auf Tour ist, ist eine öffentliche IP-Adresse oder ein DynDNS Dienstleister (Dynamic DNS Service) erforderlich. Hinweise zur Einrichtung findet man weiter unten. Sind der Öler und die Oilerbase gewöhnlich im gleichen Netz eingebucht, kann dieser Schritt ausgelassen werden. 

Um mit dem Öler zu kommunizieren, wurden einige PHP Scripte erstellt, die hier zu finden sind. Die Funktionen auf dem Öler und die Scripte auf dem Web-Server sind eng miteinander verzahnt.  Z.B. ziehen Änderungen an den Öler Funktionen sehr wahrscheinlich Änderungen an den Skripten nach sich und umgekehrt.

Die Konfiguration der Oilerbase ist recht einfach - im Grunde werden nur Standardfunktionen genutzt. Nachfolgend die einzelnen Schritte, um einen Rasberry Pi (z.B. das Modell Raspberry Pi 3 Modell B+) in Betrieb zu nehmen.

### Betriebssystem installieren

Die mittlerweile einfachste Methode ist die Verwendung vom [Raspberry Pi Imager](https://www.raspberrypi.com/software/). Bereits vor dem Beschreiben der SD-Karte können alle wichtigen Einstellungen vorgegeben werden:
- Hostname
- ssh
- Benutzername/Passwort
- WLAN Einstellungen
- Tastatur
- Zeitzone

Dann nur noch das gewünschte Betriebssystem wählen ("Raspberry Pi OS Lite" reicht in unserem Fall) und die SD-Karte wird während des Downloads gleich beschrieben.

Nach Fertigstellung sollte der RPi nun eine Anmeldung akzeptieren. Dies kann man unter Windows entweder mit [putty](https://www.putty.org/) oder auch mit der in Windows 10 eingebauten OpenSSH (=Open Secure Shell) bewerkstelligen. Hier mal die OpenSSH Variante (dazu Konsole oder Eingabeaufforderung starten oder mit der Tastenkombination \<Windows>+r den "Ausführen" Dialog). Dann folgenden Befehl eingeben (host und user ändern, wie oben konfiguriert):

  `ssh <user>@<host>` 

  Eventuelle Warnmeldungen bezüglich ECDSA host keys mit 'yes' beantworten.

  Nach der Anmeldung zunächst mal die letzten Updates einspielen:

  ```
  sudo apt update
  sudo apt upgrade
  ```
  
[**Optional**] Willkommensbildschirm ändern, damit wir bei Anmeldung entsprechend begrüßt werden. Dazu Datei "/home/pi/.profile" bearbeiten. Also: `nano ~/.profile`, dann ans Ende der Datei und dort mit rechter Maustaste die folgenden Zeilen aus der Zwischenablage einfügen (andere "Schriftarten" s. [hier](http://patorjk.com/software/taag)):

  ```
  cat << 'EOF'
  
                      _  __ _  ____  _ _           ____
        Welcome to   (_)/ _(_)/ __ \(_) |         |  _ \
            __      ___| |_ _| |  | |_| | ___ _ __| |_) | __ _ ___  ___
            \ \ /\ / / |  _| | |  | | | |/ _ \ '__|  _ < / _` / __|/ _ \
             \ V  V /| | | | | |__| | | |  __/ |  | |_) | (_| \__ \  __/
              \_/\_/ |_|_| |_|\____/|_|_|\___|_|  |____/ \__,_|___/\___|
  
  EOF
  ```

### Apache Web Server installieren

#### Installation des Apache Web-Servers

`sudo apt install apache2`

Nach erfolgreicher Installation kann man schon die Standardseite des Webservers aufrufen. Hier den oben gewählten Hostnamen nutzen, z.B.

`http://oilerbase`

#### Apache Web Server absichern

`sudo nano /etc/apache2/apache2.conf`

Dort folgende Änderungen vornehmen. Sind die Schlüsselwörter schon vorhanden, dort ändern oder wenn sie nicht existieren, am Ende der Datei hinzufügen. Der Servername kann frei gewählt werden und muss nicht mit dem oben gewählten Hostnamen übereinstimmen:

```
# Keine Details zum Server anzeigen
ServerSignature Off
ServerTokens Prod
ServerName oilerbase
```

Folgenden Abschnitt löschen, da wir das Verzeichnis /usr/share nicht verwenden:

```
<Directory /usr/share>
    AllowOverride None
    Require all granted
</Directory>
```

Folgenden Abschnitt ändern. Wichtig sind die Minuszeichen vor den Optionen. "-Indexes" verhindert z.B. die automatische Anzeige von Verzeichnislisten, wenn im angewählten Ordner keine "index.html" Datei gefunden wird. "FollowSymLinks" schließen wir aus, da wir keine Links verwenden. Wir könnten auch die ganze Zeile ersetzen mit: `Options none`. Allerdings ist es oft sinnvoll, bestimmte Optionen bewusst auszuschließen (z.B. wenn sie beim übergeordneten Verzeichnis erlaubt wurden):

```
<Directory /var/www/>
    Options -Indexes -FollowSymLinks
    AllowOverride None
    Require all granted
</Directory>
```

Datei speichern und Editor verlassen. 

Die Apache Konfiguration kann mit folgendem Befehl geprüft werden:

`sudo apachectl configtest`

#### Verzeichnisstruktur einrichten

Als nächstes bauen wir die Verzeichnisstruktur für unseren Webserver auf:

```
sudo rm /var/www/* -R
sudo mkdir /var/www/html
sudo mkdir /var/www/update
sudo mkdir /var/www/update/WemosMini
sudo mkdir /var/www/uploads
sudo mkdir /var/www/log
sudo chmod 755 /var/www -R
sudo chmod 757 /var/www/uploads
```

### Installation von Samba

Um einfacher auf die Dateien zugreifen zu können, installieren wir noch Samba. Außerdem benötigen wir PHP für den Web-Server (bzw. zur Ausführung der Scripte hier im Verzeichnis):

`sudo apt install php samba`

Samba muss konfiguriert werden:

`sudo nano /etc/samba/smb.conf`

In dieser Datei werden am Ende einige Zeilen hinzugefügt, um das Verzeichnis des Webservers 'zugänglich' zu machen:

```
[oilerweb]
  path=/var/www
  read only = no
```

Editor beenden und mit folgendem Befehl ein Passwort für die Freigabe setzen. Dieses Passwort wird benötigt, um das Verzeichnis unter Windows einzubinden (zu mounten):

`sudo smbpasswd -a root` (und zweimal Passwort eingeben)

#### Verzeichnis unter Windows einbinden

Danach dann unter Windows (in einer Eingabeaufforderung oder Konsole) mit dem oben gewählten Passwort (entsprechend ändern):

`net use * \\oilerbase\oilerweb <passwort> /user:root /persistent:yes`

Die Ausgabe sollte so oder ähnlich lauten:

> ```
> Laufwerk Z: ist jetzt mit \\oilerbase\oilerweb verbunden.
> 
> Der Befehl wurde erfolgreich ausgeführt.
> ```

nun können wir die hier aufgelisteten Dateien in das entsprechende Verzeichnis kopieren (nach unserem Beispiel Z:\html). 

Wenn Z: im weiteren Verlauf verwendet wird, steht es beispielhaft für den Laufwerksbuchstaben, der beim net use Befehl (s.o.) zugewiesen wurde.

Und nun der erste Test: Browser starten und Adresse der Oilerbase eingeben:

`http://oilerbase/oilerbase.php` oder `http://oilerbase.fritz.box/oilerbase.php`(sollte auch gehen, wenn eine Fritz.box im Einsatz ist). Als Ergebnis wird ein einfaches OK oben links auf einer leeren Seite angezeigt.

### Öler testen

Um den Öler zu testen (wenn dieser schon betriebsbereit und konfiguriert ist) können folgende Aktionen durchgeführt werden:

**Test der "Update Oiler" Funktion**: Ordner im Update Verzeichnis anlegen, der eine höhere Versionsnummer hat, als der Öler. Also z.B. Z:\update\WemosMini\4.9.999

Ein/zwei kleinere Dateien in diesen Ordner kopieren (ist eigentlich egal, sollte aber nicht den bestehenden Dateien auf dem Öler namentlich in die Quere kommen). Also z.B. "test.txt" oder "beispiel.dat".

Dann die Update Funktion des Ölers aufrufen. Die Dateien sollten ohne Fehlermeldung transferiert werden. Ist dies der Fall, dann die Dateien über den File Browser des Ölers wieder löschen (sie stören eigentlich nicht, nehmen aber Platz weg).

Im Falle eines Fehlers sollten die Logs des Webservers überprüft werden. Man findet sie normalerweise in /var/log/apache2. Zusätzlich kann die Ausgabe des Ölers helfen. Dazu im Öler ggf. die Funktion "Logging to file?" anschalten (s. Konfiguration) und die Aktion wiederholen. Danach findet man im File Browser die Datei "myLogger.txt" und ein Klick darauf zeigt den Inhalt im Editor Fenster an. ACHTUNG: nicht vergessen, die "Logging to file" Option wieder auszuschalten!

**Test der "Upload Tracks" Funktion**: im File Browser des Ölers zwei Dateien erzeugen mit Namensmuster der Track Dateien (z.B. "/20210614-1523.dat" und "/20210615-1245.dat"). Dazu den Namen in das Eingabefeld eintragen, dann "New file" drücken, etwas in das Editorfenster eintragen und "Save" drücken). Nun im Hauptmenü die Funktion "Upload Tracks" wählen.

### Oilerbase veröffentlichen

"Veröffentlichen" hört sich etwas hochtrabend an, gemeint ist damit die Bereitstellung der Oilerbase im großen, weiten Internet, damit der Öler von unterwegs darauf zugreifen kann. Dazu benötigt die Oilerbase eine eindeutige IP-Adresse, damit sie eindeutig identifiziert werden kann. Da fest zugewiesene IP Adressen knapp sind und man als Otto Normalverbraucher auch keine gebucht hat (ja, das kostet Geld), kann man einen sogenannten DynDNS Service in Anspruch nehmen (der durchaus kostenlos nutzbar ist). Dieser Service bekommt von unserem "Internet Router", der von unserem Provider täglich mit einer anderen IP-Adresse versorgt wird, diese IP-Adresse jedes Mal nach Änderung mitgeteilt. So kann er immer die richtige IP-Adresse rausgeben, wenn er im Internet danach gefragt wird. Der so gefundene Internet Router leitet die Anfrage des Ölers dann weiter an die Oilerbase und schon haben sich beide gefunden...

Wie dieses DynDNS nun auf dem eigenen Internet Router eingerichtet wird, ist vom Hersteller abhängig. 

Sie ähneln sich aber in den meisten Fällen darin, dass entweder ein DynDNS Anbieter aus einer Liste ausgewählt wird oder eine Update URL angegeben werden muss. Dazu werden noch die Anmeldedaten eingegeben, die man zur Erstellung eines Kontos beim Anbieter verwendet hat. Fertig.

Beim jeweiligen Hersteller des eigenen Routers sollte eine Beschreibung zur Einrichtung eines DynDNS Dienstes zu finden sein. Manche Router Hersteller bieten sogar selber einen kostenlosen DynDNS Service für ihre Kunden an. Ansonsten findet man diese Dienste im Internet, wenn man z.B. nach "DynDNS kostenlos" sucht. Bei dem von mir anfangs gewählten Anbieter musste einmal im Monat (Erinnerung per E-Mail) die freie Nutzung bestätigt/verlängert werden (dafür gab's coole Domain Namen).

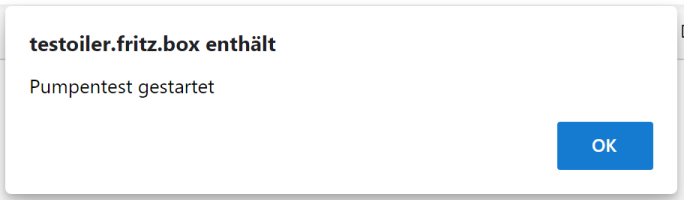
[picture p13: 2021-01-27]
docs/images/msgpmptst.png

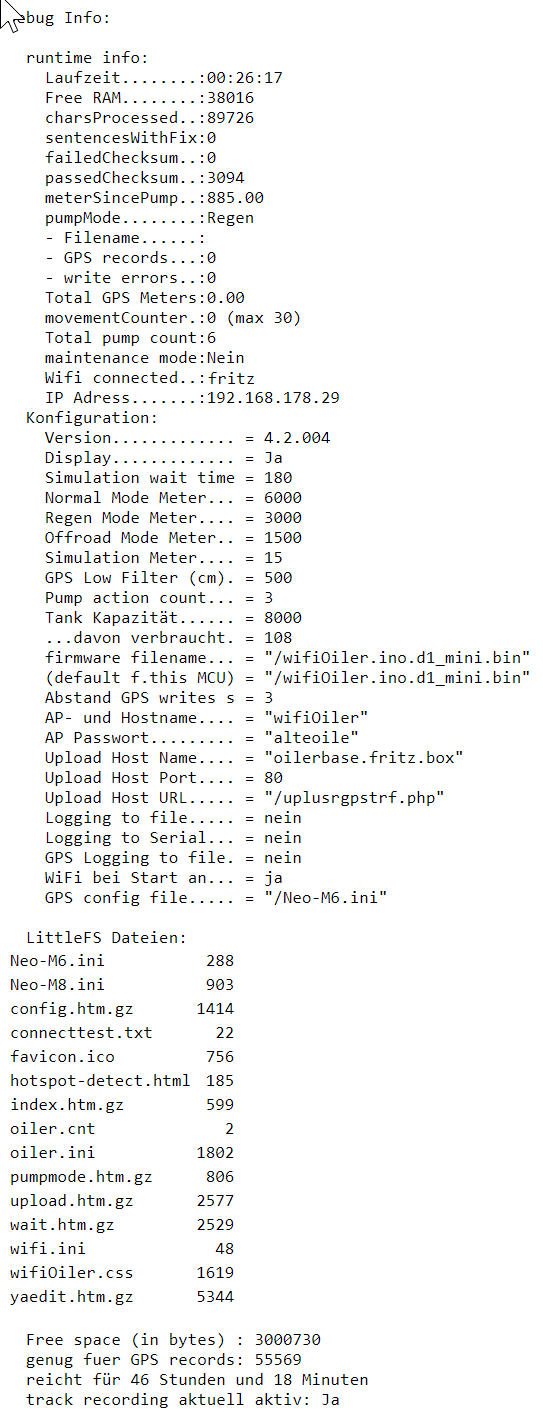
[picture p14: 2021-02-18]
docs/images/scrdbginf.png

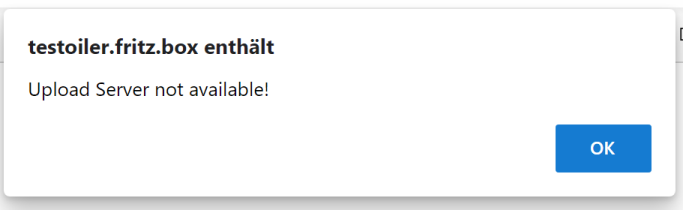
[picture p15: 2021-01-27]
docs/images/msguplsrv.png

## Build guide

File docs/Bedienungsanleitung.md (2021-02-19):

# Bedienung des Ölers
Der Öler kann über eine Web-Oberfläche bedient werden. Dafür wurde auf dem ESP8266 Chip ein kleiner Web-Server implementiert. 

Kleiner Hinweis zur Performance: der Öler ist ständig mit dem Empfang und der Auswertung der GPS Daten beschäftigt, so dass manchmal etwas Geduld erforderlich ist, da eine Reaktion des Web-Servers schon mal einige Sekunden dauern kann - also nicht nervös werden und Reaktion des Browsers abwarten. Tippt man hektisch auf den Buttons herum, bringt das den kleinen Rechenknecht nur in Schwierigkeiten... Insgesamt sind die Antwortzeiten aber durchaus anständig.

## WLAN Aktivierung
Nachdem der Öler gestartet wurde, kann er über eine Web-Oberfläche bedient werden. Ist der Öler so konfiguriert (s. Einstellungen), dass das WLAN automatisch aktiviert wird, ist sonst nach dem Start keine Aktion erforderlich. Muss dagegen das WLAN manuell aktiviert werden, wird der Button so lange gedrückt, bis die LED rot leuchtet (dies ist das Zeichen dafür, dass ein langer Tastendruck erkannt wurde).
<br>Bei Aktivierung des WLANs versucht der Öler, sich mit einem der in der Datei "wifi.ini" konfigurierten WLAN Netze zu verbinden. Ist dies nicht möglich, wird ein eigener Access Point aktiviert, an dem man sich anmelden kann. Name und Passwort des Access Points wird in den Einstellungen konfiguriert (s. Konfiguration). <br>Ist ein Display angeschlossen, zeigt die WLAN Statusanzeige nun ein 'w' für ein verbundenes WLAN oder ein 'A' für einen erstellten Access Point. Ohne Display wird das Ergebnis durch ein LED Feedback angezeigt (mehrmaliges grünes Flackern für WLAN, erst rotes dann grünes Flackern für einen Access Point).
<br>Bei Auslieferung heißt der Access Point "wifiOiler" und das Passwort "alteoile". Dies sollte in den Einstellungen bald geändert werden, damit nicht jemand anderes am Öler Einstellungen ändern kann.
## Hauptmenü der Web-Oberfläche
Im oberen Teil wird der Name des Ölers (ist identisch mit dem Namen des Access Points) und die Version angezeigt. Danach sind mehrere Buttons zu sehen:
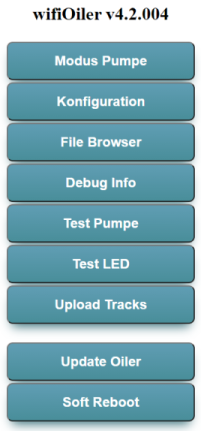
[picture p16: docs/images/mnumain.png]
Main Menu
<br>
### Modus Pumpe
Ein Untermenü mit den einstellbaren Modi erscheint. Die aktuelle Einstellung wird durch einen roten Button angezeigt. Wählen kann man
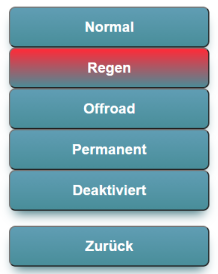
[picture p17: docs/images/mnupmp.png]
Pump Menu
<br>
<br>Nach welchen Entfernungen bei den einzelnen Modi geölt wird, kann in den Einstellungen konfiguriert werden. Üblicherweise wird bei **Regen** deutlich öfter geölt, als bei trockener Straße (also **Normal**), da die Nässe das Öl von der Kette wäscht. Bewährt hat sich bei mir die zweifache Menge. Wenn im Normalzustand also alle 6000 Meter geölt wird, ist bei Regen ein Wert von 3000 Meter ein guter Richtwert.
<br>Bei **Offroad** Fahrten sollte noch öfter geölt werden, damit an der Kette haftender Dreck nicht wie Schmirgelpapier wirkt.
<br>Der Modus **Permanent** kann verwendet werden, wenn das System enlüftet werden soll (z.B. nach dem Einbau). Eine manuelle Entlüftung sollte allerdings zuerst vorgenommen werden, damit die Pumpe nicht stundenlang im Dauerbetrieb ist.
<br>Den Modus **Deaktiviert** verwende ich eigentlich nur zum Testen oder Debuggen.
<br>Da man während der Fahrt nicht das Handy aus der Tasche ziehen kann (bzw. sollte!), wird der Pumpenmodus dann über den eingebauten Button umgestellt. Dabei wird jeweils pro Knopfdruck ein Modus weitergeschaltet, von **Normal** zu **Regen**, dann zu **Offroad**, dann **Permanent**, dann aus und danach wieder zu **Normal**. 
<br>Nach jedem Knopfdruck wird die gewählte Pumpeneinstellung durch ein LED Signal angezeigt
* 1 x grün = **Normal**
* 2 x grün = **Regen**
* 3 x grün = **Offroad**
* 4 x grün = **permanent**
* 1 x rot = **aus**
<br>Genau 1,5 Sekunden nach dem letzten Knopfdruck wird die gewählte Einstellung aktiv. Durch diese Verzögerung können die Modi durchgeschaltet werden, ohne dass gleich die Pumpe ausgelöst wird.
### Konfiguration
In diesem Dialog lassen sich die Einstellungen des Ölers dauerhaft ändern. Die einzelnen Einstellungen sind nochmal separat [hier](Einstellungen.md) beschrieben.
### File Browser
Ein File Browser für die Dateien im Dateisystem des ESP8266, welches für Konfigurationsdateien, HTML-Sourcen für den Web-Server und für die aufgezeichneten Touren (Track files) verwendet wird. Es sind auch Editierfunktionen vorhanden, um z.B. die WiFi-Konfiguration zu ändern, Track Files zu löschen, etc. Trotz Sicherheitsabfrage sollte man hier sehr vorsichtig sein. Löscht man versehentlich die Konfiguration oder HTML Dateien, muss das Dateisystem u.U. wieder extern 'beladen' werden (wozu der Öler ggf. ausgebaut werden muss - also Vorsicht!).
<br>Es stehen drei Varianten für den File Browser zur Verfügung (kann in den Einstellungen geändert werden). Der Standard Browser (/littlefsb.htm) verbraucht am wenigsten Platz und kann ohne Verbindung zum Internet genutzt werden. Weitere Infos s. [Einstellungen - FSBrowser & Editor](Einstellungen.md/#fsbrowser)

In der oberen Funktionsleiste sind einige Funktionen über Buttons anwählbar. Im linken Bereich sieht man eine Liste mit allen Dateien, die im Filesystem enthalten sind. Im rechten Teil, der größte Bereich im File Browser, sieht man ein Eingabefenster, in dem Dateien angezeigt und/oder geändert werden können. Wählt man mit der Maus eine Datei in der linken Liste aus, wird der Inhalt im Eingabefenster angezeigt, sofern es sich um eine editierbare Datei handelt (wird anhand der Dateiendung entschieden). Wählt man z.B. die Datei "wifi.ini" wird im Eingabefenster der Inhalt der wifi.ini, also die wifi Konfiguration angezeigt.

Vorsicht: hat man im Eingabefenster eine Datei geändert und diese noch nicht gespeichert, wird mit einem Klick auf eine Datei in der Liste die Änderung ohne Rückfrage verworfen.

Die einzelnen Funktionen im File Browser:

- #### Upload

  Über den Button **[Datei auswählen]** kann eine Datei aus dem lokalen Dateisystem (also PC oder Notebook) ausgewählt werden. Der Name der ausgewählten Datei erscheint nun neben dem **[Datei auswählen]** Button und im Eingabefeld in der Funktionsleiste. Mit dem Button **[Upload]** kann diese Datei jetzt in das Dateisystem auf dem Öler hochgeladen werden. Wenn erforderlich, kann der Name der Datei vor dem Hochladen im Eingabefeld noch geändert werden - die hochgeladene Datei wird dann unter diesem neuen Namen auf dem Öler abgespeichert. 

  Während des Uploads blinkt die LED des Ölers. Je schneller die LED blinkt, desto schneller ist der Upload. Auf einem angeschlossenen Display werden ebenfalls Statusmeldungen zum Upload angezeigt. Ist die Datei komplett hochgeladen, wird die Eingabe in der Funktionsleiste zurückgesetzt und der Name der hochgeladenen Datei ist in der Liste sichtbar und wird hervorgehoben.

  Mit **[Upload]** kann auch eine neue **Firmware** eingespielt werden. Dazu in der Arduino IDE den wifiOiler Sketch laden und mit der Funktion "Sketch" -> "Kompilierte Binärdatei exportieren" die Firmware Datei erzeugen. Die Datei wird im Sketch Verzeichnis abgelegt, also in der IDE die Funktion "Sketch" -> "Sketch Ordner anzeigen" wählen. Im angezeigten Ordner findet man nun eine Datei mit dem Namen "wifiOiler.ino.d1_mini.bin". 

  Lädt man diese Datei mit der **[Upload]** Funktion hoch, wird automatisch erkannt, dass eine Firmware hochgeladen wurde und der Updateprozess wird automatisch gestartet. Die Firmware wird anhand des Namens erkannt (s. Konfiguration, dort wird der Name angegeben, wonach der Öler Ausschau halten soll).

- #### Save

  Mit dieser Funktion wird grundsätzlich der Inhalt des Eingabebereichs unter dem Dateinamen gespeichert, der im oberen Rahmen des Eingabebereichs angezeigt wird. Existiert diese Datei, wird sie mit dem neuen Inhalt überschrieben. **[Save]** funktioniert dabei wie ein Upload (LED und Displayanzeige wie beim Upload, s.o.). Es wird keine Bestätigung angezeigt (außer im Display).

- #### New File

  Mit diesem Button kann eine neue Datei angelegt werden, wenn der Name zuvor im Eingabefeld in der Funktionsleiste angegeben wurde. Nach der Anlage erscheint der Name links in der Liste, das Eingabefeld wird geleert und die neue Datei kann editiert werden. Dies funktioniert auch mit Dateien, deren Endung nicht auf eine Textdatei schließen und sich sonst nicht editieren lassen. 

- #### Rename

  Im Dateisystem existierende Dateien können auch umbenannt werden. Dazu die Datei auswählen, die umbenannt werden soll, den neuen Namen in das Eingabefeld in der Funktionsleiste eintragen und anschließend **[Rename]** drücken.

- #### Delete

  Wie die Beschriftung vermuten lässt, kann man mit dieser Funktion Dateien aus dem Dateisystem des Ölers löschen. Dazu die Datei links in der Liste auswählen und danach **[Delete]** drücken. Nach einer Sicherheitsabfrage wird die Datei endgültig gelöscht (wenn die Aktion nicht abgebrochen wird).

  Eine letzte Rettung besteht nur für Dateien, deren Inhalt noch im Eingabefenster angezeigt wird. Da der Inhalt und der Dateiname (im oberen Rahmen des Eingabebereichs) noch existieren, kann mit der [Save] Funktion die Datei mit dem aktuell angezeigten Inhalt gesichert und damit wiederhergestellt werden.

- #### Download

  Eine links in der Liste ausgewählte Datei kann mit dieser Funktion auf den PC oder anderes Endgerät, mit dem man gerade den Öler bedient, heruntergeladen werden. Es wird immer der gesicherte Zustand genutzt. Eventuelle Änderungen im Eingabebereich werden nicht heruntergeladen - dazu die Datei vorher sichern.

- #### Extract

  Viele oder alle der bereitgestellten HTML-Dateien für den Öler sind mit 'gzip' komprimiert worden, um Speicherplatz zu sparen. Mit dieser Funktion können diese komprimierten Dateien dekomprimiert werden. Dabei wird davon ausgegangen, dass nur jeweils EINE Datei im Archiv vorhanden ist, die unter dem Namen des Archivs (ohne abschließendes ".gz") im Dateisystem des Ölers gesichert wird.

  Eine dekomprimierte Datei wird bei der Verwendung durch den Öler immer der komprimierten Datei vorgezogen. Wenn also z.B. "upload.htm.gz" per **[Extract]** dekomprimiert wird und danach zusätzlich eine Datei "upload.htm" existiert, wird bei Anwahl der Upload Funktion im Hauptmenü des Ölers die "upload.htm" Datei genutzt und nicht mehr die "upload.htm.gz". Dies hat den Vorteil, dass gewünschte Änderungen sofort aktiv sind. 

### Debug Info
Hier werden Laufzeit Informationen, die aktuelle Konfiguration und der Inhalt des Dateisystems angezeigt. Außerdem wird hier die restliche Speicherkapazität angezeigt und die (mit der aktuellen Konfiguration) verbleibende Aufzeichnungszeit.
### Test Pumpe
Hiermit kann man testen, ob der Öler richtig aufgebaut und angeschlossen wurde. Die Pumpe wird so oft ausgelöst, wie in der Konfiguration vorgegeben (Anzahl Pumpaktionen pro Ölvorgang).
### Test LED
Die LED blinkt dreimal grün und dreimal rot. So kann festgestellt werden, ob die zweifarbige LED richtig angeschlossen wurde.
### Upload Tracks
Ist ein Upload Server vorhanden, können die aufgezeichneten Tracks hochgeladen werden. Nach erfolgreichem Upload werden sie im Öler Dateisystem gelöscht, um den Speicherplatz wieder freizugeben. Siehe Dokumentation zur [Oilerbase](../OilerBase/readme.md).
### Update Oiler
Ist die Oilerbase implementiert, kann von dieser ein Update geladen und installiert werden (es gibt allerdings auch andere Wege). Siehe Dokumentation zur [Oilerbase](../OilerBase/readme.md).
### Soft Reboot
Mit dieser Funktion kann der Öler neu gestartet werden. Normalerweise überflüssig, kann man aber mal verwenden, wenn man die Einstellungen per Editor geändert hat und diese aktiv werden sollen.

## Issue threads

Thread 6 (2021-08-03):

Automatic switching off of continuous pumping while driving does not work.

volw, 2021-08-03:
Automatic switching off of continuous pumping while driving does not work.
Pump continues to run permanently.

volw, 2021-08-03:
fixed - moved movement check to (pump) trigger function

Closed 2021-08-03.

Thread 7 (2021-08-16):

About 25% of all uploads (track) fail

volw, 2021-08-16:
May be check if file has arrived is too fast. apache/php is storing the file at a temp location and moving it from there to original location. If check is faster than that, upload is recognized as failed, although the file arrived.

volw, 2021-08-16:
Implemented multiple checks (max 3). This will slightly increase traffic - doesn't matter
Done. Tests OK...

Closed 2021-08-16.

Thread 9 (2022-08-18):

Uploading gps tracks from different bikes to same oilerbase

volw, 2022-08-18:
If you upload the recorded routes of several motorbikes to one oilerbase, you can no longer distinguish the files afterwards. It would be good if you could make a setting on the oiler.

volw, 2022-08-18:
New setting (gts), file upload tested... (header adjustment needed), track conversion testing still pending

Closed 2022-08-18.

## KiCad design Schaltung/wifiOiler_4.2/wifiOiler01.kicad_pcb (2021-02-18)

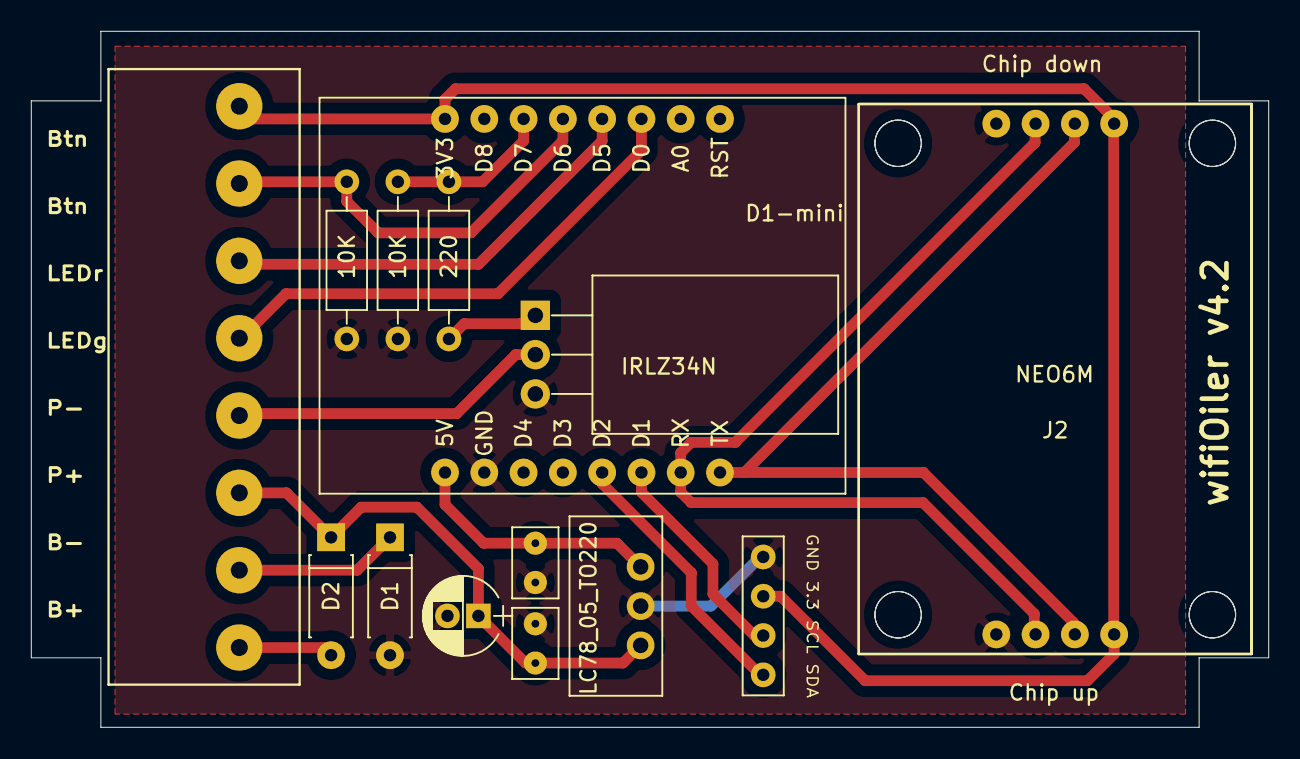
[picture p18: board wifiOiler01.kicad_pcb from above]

Board: 2 copper layers, 80.0 x 45.0 mm, 15 parts (0 on the bottom side), 16 nets.

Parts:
C1, C2: CP_Small; MKS02-63 100N Folienkondensator
C3: 10 uF; CP_Radial_D5.0mm_P2.00mm
D1, D2: 1N4004; D_DO-41_SOD81_P7.62mm_Horizontal
J1: Conn_01x04; Pin_Header_Straight_1x04_Pitch2.54mm
J2: Conn_01x04; NEO6M_18_ChipUp
MCU1: D1-mini; D1 mini (ESP8266)
N1: NEO6M; NEO6M_18_ChipDown
P1: CONN_01X08; Stiftleiste_1x8_5mm_D13_Box_korr
Q1: IRLZ34N; TO-220-3_Horizontal_NoPad
R1: 220; R_Axial_DIN0207_L6.3mm_D2.5mm_P10.16mm_Horizontal
R2, R3: 10K; R_Axial_DIN0207_L6.3mm_D2.5mm_P10.16mm_Horizontal
U1: LC78_05_TO220; LC78_0.5 aufrecht

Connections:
unnamed: C1.1, MCU1.16, U1.3
unnamed: C1.2, C2.2, C3.2, D1.2, J1.4, J2.4, MCU1.15, N1.4, Q1.3, R2.2, R3.2, U1.2
unnamed: C2.1, C3.1, D2.1, P1.3, U1.1
unnamed: D1.1, P1.2
unnamed: D2.2, P1.1
unnamed: J1.1, MCU1.12
unnamed: J1.2, MCU1.11
unnamed: J1.3, J2.1, MCU1.8, N1.1, P1.8
unnamed: J2.2, MCU1.9, N1.2
unnamed: J2.3, MCU1.10, N1.3
unnamed: MCU1.3, P1.5
unnamed: MCU1.4, P1.6
unnamed: MCU1.5, P1.7, R3.1
unnamed: MCU1.6, R1.1, R2.1
unnamed: P1.4, Q1.2
unnamed: Q1.1, R1.2

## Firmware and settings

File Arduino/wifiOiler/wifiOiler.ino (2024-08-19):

/************************************************************************
 * wifiOiler, an automatic distance depending motorbike chain oiler
 * Copyright (C) 2019-2024, volw
 *
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
 * You should have received a copy of the GNU General Public License
 * along with this program.  If not, see <https://www.gnu.org/licenses/>.
 ************************************************************************/
 // ACHTUNG: defines in wifioiler.h beachten!!
#include <ESP8266WiFiMulti.h>
#include <DNSServer.h>
#include <ESP8266mDNS.h>
#include <ESP8266WebServer.h>
#include <ESP8266HTTPClient.h>
#include <TinyGPS++.h>
#include "src/biLedx/biLedx.h"  // lib für nicht-modales Blinken (zweifarbiger) LEDs
#include "wifiOiler.h"
#include "LittleFSlogger.h"
#include "oilerDisplay.h"
#include "messages_de.h"
//#include "messages_en.h"
#include "globalVars.h"
#include "configuration.h"
#include "rotate.h"

/*******************************************************************
 ******************** Setup ****************************************
 *******************************************************************/
void setup() 
{    
  GVmyLedx.on(LED_GRUEN); // LED an waehrend Initialisierung
  pinMode(BUTTON_PIN, OUTPUT);
  digitalWrite(BUTTON_PIN, LOW);
    
  Serial.begin(9600);
  delay(100); // = less garbage...
  Serial.println();

  GVmyDisplay.Init();
  GVmyDisplay.PrintMessage("Init", 10000);

  bool deleteLog = false;
  if (!_FILESYS.begin()) {
    Serial.println(F(MSG_ERROR_INITIALISING_FILESYSTEM));
  } else {  // read config / rotate log / check log file size...
    GVoilerConf.read();
    if (_FILESYS.exists(LOG_FILE_NAME)) {
      // try to rotate:
      if (GVoilerConf.mrf > 0) {
        rotateFile(LOG_FILE_NAME, GVoilerConf.mrf);
      }
      // still there and too big?
      if (_FILESYS.exists(LOG_FILE_NAME)) {
        File f = _FILESYS.open(LOG_FILE_NAME, "r");
        deleteLog = (f.size() > LOG_FILE_MAX_BYTES);
        f.close();
      }
    }
  }

  // schon mal was auf's Display bringen (wird erst in Loop angezeigt über Check()):
  GVmyDisplay.PrintModeStr(getPumpModeStr(GVpumpMode));
  GVmyDisplay.PrintMeter(getModeMeters(GVpumpMode));
  GVmyDisplay.PrintKmh(0);

  GVmyDisplay.MessageAdd(".", 10000);
  GVcurrentfpw = GVoilerConf.fpw;  // merken, GVcurrentfpw bestimmt je nach Platz im FS, ob Tracks geschrieben werden...

  // Logging in Datei und Serial (sonst als 2. Parameter: false)
  // VORSICHT: falls Datei sehr groß wird, können Schreiboperationen (incl.
  // Öffnen und schließen der Datei) seeehr langsam sein und das ganze Ding ausbremsen.
  if (!StaticLogger.begin(GVoilerConf.lgf ? LOG_FILE_NAME : "", GVoilerConf.lgs)) {
    Serial.println(F(MSG_ERROR_INITIALISING_LOGGER));
  }
  StaticLogger.setLogLevel(GVoilerConf.lvl);
  GVmyDisplay.MessageAdd(".", 10000);
  
  infoPrintf(PSTR(MSG_PROGRESS_STARTING_INIT));
  if (deleteLog) warnPrintf(PSTR(MSG_CHECK_LOG_SIZE_DELETE));

  setupButton();

  //TODO: +++hier könnte noch ein Check auf Track-Dateien < x bytes erfolgen - die dann löschen

  checkforUpdate();
  GVmyDisplay.MessageAdd(".", 10000);

  checkFilesystemSpace(); // tracking deaktivieren, wenn zu wenig Platz
  GVmyDisplay.MessageAdd(".", 10000);

  // WiFi wird beim Starten ausgeschaltet und kann bei Bedarf (Button) angeschaltet werden:
  WiFi.forceSleepBegin(); // Wifi off
  GVwifiSleeping = true;

  setupGPS(); // Abfrage auf Wartungsmodus innerhalb der Funktion
  GVmyDisplay.MessageAdd(".", 10000);

  setupWebServer();
  GVhttp.setUserAgent(F(HTTP_USER_AGENT));  // only allow this user agent on oilerbase (see php scripts)
  GVmyDisplay.MessageAdd(".", 10000);

  checkTank();  // Öltank leer?

  infoPrintf(PSTR(MSG_VERSION_MESSAGE), VERSION, BOARD_TYPE);

  if (GVoilerConf.wso || GVmaintenanceMode) 
    toggleWiFi();
  else 
    GVmyLedx.off();
  GVmyDisplay.PrintMessage("wifiOiler\n  v");
  GVmyDisplay.MessageAdd(VERSION,2000);
  #ifdef _NO_PUMP_
    warnPrintf(PSTR(MSG_ATT_PUMP_DEACTIVATED));
    GVmyDisplay.PrintAckMessage("Pumpe\ndeaktiv.\n(confirm)");
  #endif
  infoPrintf(PSTR(MSG_PROGRESS_STARTING_END));
}

/*******************************************************************
 ***************** Main Loop ***************************************
 *******************************************************************/
void loop() {
  if (!GVwifiSleeping) {
    if (GVwifiAPmode) {
      GVdnsServer.processNextRequest();
    } 
    MDNS.update();
    GVwebServer.handleClient();
    checkWiFi();
  }
  GVmyLedx.checkState();  // LED-Behandlung
  GVmyPumpx.checkState(); // Behandlung Pumpe
  checkButton();          // Button Abfrage  
  checkGPSdata();         // GPS Daten lesen, falls welche da sind
  checkMovement();        // Überprüfung auf Bewegung
  GVmyDisplay.Check();    // Display handling
  
  if (GVmaintenanceMode && (millis() > (GVshowMaintMode + 10000UL))) {
    // noch ne kleine Spezialroutine, um Wartungsmodus anzuzeigen:
    GVmyLedx.start LED_SHOW_MAINTENANCE;
    GVshowMaintMode = millis();
  }
  if (GVupdateResult == UPD_REBOOT_NOW) {
    checkforUpdate();
    GVupdateResult = UPD_NOT_ACTIVE; // falls er wieder zurückkommt...
  }
}

/*******************************************************************
 ******************** Reboot ***************************************
 *******************************************************************/
void oilerReboot() {
  if (!GVwifiSleeping) {
    //MDNS.close();
    WiFi.disconnect();
    delay(500);
  }
  ESP.restart();
}

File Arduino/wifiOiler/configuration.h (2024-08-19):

/************************************************************************
 * wifiOiler, an automatic distance depending motorbike chain oiler
 * Copyright (C) 2019-2024, volw
 *
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
 * You should have received a copy of the GNU General Public License
 * along with this program.  If not, see <https://www.gnu.org/licenses/>.
 ************************************************************************/

/* To add configuration values, follow these steps:
 *  1. increment #define _LIST_LEN_ (see below)
 *  2. search for "add new option here" (5 locations below)
 *  3. add new value to config.htm (add line to aConfig array)
 */
#pragma once

#define _LIST_LEN_ 23
// #define debug_out(...) Serial.printf(__VA_ARGS__)
// no debug messages:
#define debug_out(...)
const char PROGMEM * C_OIL_COUNTER_FILE = "/oiler.cnt";
const char PROGMEM * C_CONFIG_FILE      = "/oiler.ini";
const char PROGMEM * C_CONFIG_TEMP_FILE = "/oiler.ini.new";

class ValueList {
  
  struct Item {
    char Name[4];
    bool isSet = false;
    bool get() { return isSet; }
    void set(bool _value) { isSet = _value; }
  };

  // add new option here (1/5):
  Item ValueList[_LIST_LEN_] = {
    {"apn"},{"app"},{"bac"},{"ffn"},{"fpw"},{"gdl"},{"glf"},{"gts"},{"lgf"},{"lgs"},
    {"lvl"},{"mrf"},{"nmm"},{"omm"},{"otk"},{"pac"},{"rmm"},{"sim"},{"uhn"},{"uhp"},
    {"url"},{"wso"},{"wts"}
  };

  public:
    void setAll(bool _value) {
      for (uint8_t i = 0; i < _LIST_LEN_; i++) {
        ValueList[i].isSet = _value;
      }
    }
    bool set(const char * name, bool value) {
      uint8_t i = 0;
      while (i < _LIST_LEN_ && strcmp(ValueList[i].Name, name) != 0) i++;
      if (i >= _LIST_LEN_) return false;
      ValueList[i].set(value);
      return true;
    }

    bool getFirst(bool _value, char **foundItem) {
      uint8_t i = 0;
      while (i < _LIST_LEN_ && ValueList[i].get() != _value) i++;
      bool result = (i < _LIST_LEN_);
      if (result) *foundItem = ValueList[i].Name;
      return result;
    }
} static valueList;

class Configuration {
  public:
    String   apn = "wifiOiler";       // Name eigener Access Point
    String   app = "alteoile";        // Passwort eigener Access Point
    String   bac = "";                // base64 encoded "user:password", empty if no auth. needed
    String   ffn = UPDATE_FILE;       // Name der Firmware Datei (wird beim Upload erkannt und Update wird autom. ausgelöst)
    uint8_t  fpw = 3;                 // Fixpunktabstand beim Schreiben der Tracks in Sekunden (0=no tracks)
    bool     gdl = false;             // GPS Debug logging to file (/gpsLog.txt)
    uint16_t glf = 500;               // GPS Low-Filter
    String   gts = "20";              // track file filename prefix (if more bikes than oilerbases ;-)
    bool     lgf = true;              // file logging activated
    bool     lgs = true;              // Serial logging activated
    uint8_t  lvl = _LOG_INFO_;        // Log Level (default = info)
    uint8_t  mrf = 3;                 // max. log files (file rotation)
    uint16_t nmm = 6000;              // Normal Mode Meters
    uint16_t omm = 1500;              // Offroad Mode Meters
    uint16_t otk = 8000;              // Tank Kapazität
    uint16_t pac = 3;                 // Pump Action Count (Anzahl Pumpaktionen pro Ölvorgang)
    uint16_t rmm = 3000;              // Regen Mode Meters
    uint16_t sim = 20;                // Simulation Meter (Notprogramm)
    String   uhn = "volw.no-ip.biz";  // Upload Server
    uint16_t uhp = 80;                // Port des Upload Servers
    String   url = "/oilerbase.php";  // php file of oilerbase
    uint16_t use = 0;                 // ..davon verbraucht (wird nicht in config file gespeichert!!)
    bool     wso = true;              // WiFi beim Starten automatisch an (true) oder aus (false)?
    uint16_t wts = 180;               // Wartezeit Simulation (s)
    /* -------------------------------------------------------*/
    // add new option here (2/5) as member of class "Configuration":
    
    void read() { this->fworker(true); }
    void write() { this->fworker(false); }
    bool updateOilCounter(){  // must be public
      outFile = _FILESYS.open(C_OIL_COUNTER_FILE, "w");
      if (outFile) {
        outFile.write((const uint8_t *)&this->use, sizeof(this->use));
        outFile.close();
        return true;
      } 
      return false;      
    }
    String getJSON()
    {
      String output = "{\"apn\":\"" + String(this->apn) + "\"";
      output += ",\"app\":\"" + String(this->app) + "\"";
      output += ",\"bac\":\"" + String(this->bac) + "\"";
      output += ",\"ffn\":\"" + String(this->ffn) + "\"";
      output += ",\"fpw\":\"" + String(this->fpw) + "\"";
      output += ",\"gdl\":\"" + String(this->gdl) + "\"";
      output += ",\"glf\":\"" + String(this->glf) + "\"";
      output += ",\"gts\":\"" + String(this->gts) + "\"";
      output += ",\"lgf\":\"" + String(this->lgf) + "\"";
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

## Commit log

2021-02-02 License added
    [configuration.h]
2021-02-02 License stuff
    [configuration.h]
2021-02-04 code restructured
    [configuration.h]
2021-02-05 messages extracted to messages include
    [configuration.h]
2021-02-22 fixed delay in mode permanent
    [GPS.ino]
2021-02-22 delayed start of LED response
2021-03-15 pump & led test, file list with size
2021-03-18 FSbrowser- and reboot- services
    [FSBrowser.ino, webHandler.ino]
2021-03-30 gps config removed
    [configuration.h]
2021-04-07 runtime info - pump mode bug
    [webHandler.ino, wifiOiler.h]
2021-04-15 Initial Load
    [configuration.h]
2021-04-16 4.2.016: some corrections
    - modified config.htm (menu after save)
    - adjust message (GPS Initialisation)
    - double buffer size (update upload)
    - messages file upload (update)
    [messages_de.h, messages_en.h, update.ino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]
2021-04-20 working...
    impl. conf. param "bac" for user credentials (user:password). credentials will be passed to oiler as base64 encoded string and is decoded for config.html
    [configuration.h]
2021-05-27 Header Bug uploading tracks
    printf("...\n") was used -> use \r\n instead -> printf("...\r\n")
    otherwise apache will report 400 error (parsing header)
    spend 4 hours with debugging (during corona - so don't mind)
    [globalVars.h, upload.ino]
2021-05-28 4.2.018 bug fix parsing update info
    [update.ino, upload.ino, webHandler.ino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]
2021-05-31 4.2.019 bug in getUpdateInfo() (wrong handling for empty result)
    [update.ino, wifiOiler.h]
2021-08-03 4.2.021: fixed movement bug (Issue #6)
    moved movement check to trigger function (where it belongs ;-)
    [GPS.ino, oiler.ino, wifiOiler.h]
2022-08-18 GPS Track Filename Prefix
    [configuration.h]
2022-08-24 4.2.024 checking options
    [configuration.h]
2022-09-12 config updated
    [configuration.h]
2022-09-14 Update 4.2.025
    Track Upload Fixed (http response 400 & 499 on nginx)
    Save _all_ config params in oiler.ini (not only already saved params)
    [wifiOiler.h]
2022-09-14 pumpmode page updated
2022-09-15 updated board #defines
    [configuration.h]
2022-09-22 Update Copyright Note
    [configuration.h]
2023-02-16 shutdown wifi before reboot
    Beim Wechsel von WLAN auf Access Point konnte regelmäßig kein Access Point beim ersten Start erstellt werden
    [update.ino, webHandler.ino, wifiOiler.ino]
2023-02-23 Remove fs-browser option
    choose fs-browser html with define FS_BROWSER_URL
    [configuration.h]
2023-03-02 switch to Update.writeStream()
2023-03-03 board type in runtime info
2023-03-06 ValueList corr, http error (isServerAvailable())
    [messages_de.h, messages_en.h]
2023-03-09 input to buttons
2023-03-09 input -> button (binary)
2023-03-13 4.2.029 response improvements
    added spinner - less messages, (c) update, html validated
    [configuration.h]
2023-03-21 remove inline style download frame
2023-06-07 not yet completed...
    [configuration.h]
2023-06-17 last moves to printf macros
    [configuration.h]
2023-06-17 new config
    [configuration.h]
2023-06-28 Log file rotation
    [configuration.h]
2023-06-29 HTML check for uploaded firmware
    check for uploaded firmware in fsbrowser
    new webhandler for /checkupd
    bool reboot in checkforUpdate not needed
    [configuration.h]
2023-07-13 make logger static, move printf macros to logger
    [configuration.h]
2023-08-18 seconds between track points fix
    [GPS.ino, wifiOiler.h]
2024-08-19 update copyright notice
    [configuration.h]
2025-03-25 detail message connect error
    404 message in isServerAvailable()
    [messages_de.h, messages_en.h, upload.ino]

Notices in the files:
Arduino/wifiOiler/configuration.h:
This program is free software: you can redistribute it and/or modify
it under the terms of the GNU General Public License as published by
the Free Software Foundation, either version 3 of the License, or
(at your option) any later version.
